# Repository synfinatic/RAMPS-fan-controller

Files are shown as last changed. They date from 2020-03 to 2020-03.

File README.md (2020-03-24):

# RAMPS v1.4 Fan and Analog Expansion Board

## Warning

This board is currently untested.  Manufacture & try at your own risk!

## What?

This board adds six (6) PWM controlled MOSFETs for controlling fans or LED's
and two analog inputs to your RAMPS v1.4 board.  It takes over the SERVOS and
AUX-1 ports on your RAMPS, leaving AUX-2 and AUX-3 available for other uses.

The board is designed to allow for +5-24V input to power your fans/LEDs/etc 
while the two analog connectors expose +5V from the RAMPS.

## Why?

I have a Flashforge Creator X (Makerbot Replicator 2X clone) with an additional
part cooling fan which I wanted to switch to using a RAMPS setup instead of the
rather outdated Mightyboard running Sailfish.  This printer supports dual extruders
so I wanted additional PWM controlled 24V outputs since the heated build plate and
hot ends would eat the 3 built into the RAMPS board.

Hence my config is:

 - Heated bulid plate: D8
 - E0 hot end: D9
 - E1 hot end: D10
 - E0 fan: D11 *
 - E1 fan: D6 *
 - Part cooling fan: D5 *
 - R channel on RGB Led: D4 *
 - G channel on RGB Led: D1 *
 - B channel on RGB Led: D0 *
 - E0 thermocouple amplifier: A4 *
 - E1 thermocouple amplifier: A3 *

* Notes connections to the expansion board

## Board Images

### Top
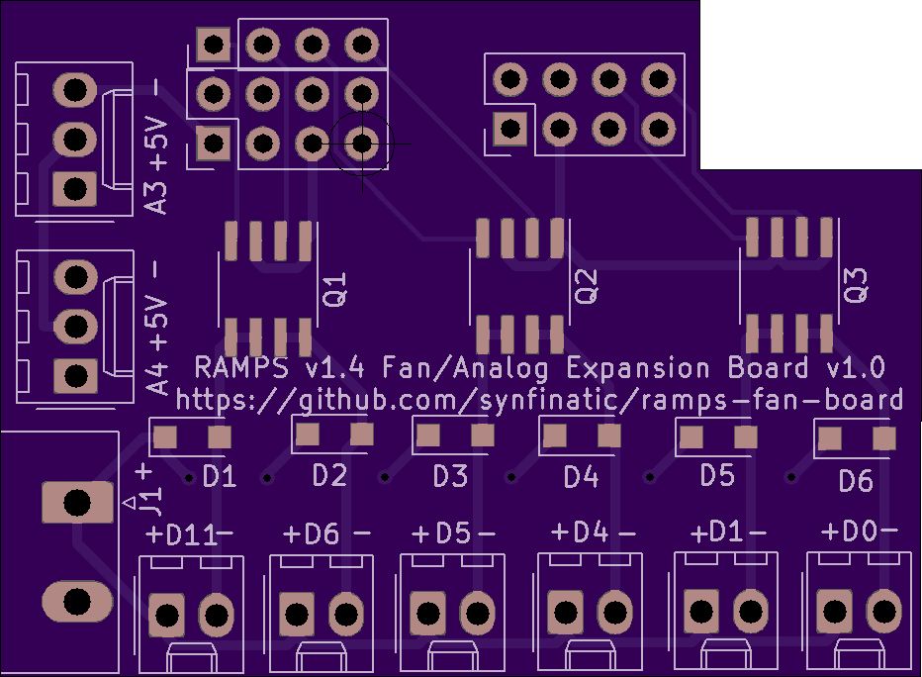
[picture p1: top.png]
top


### Bottom
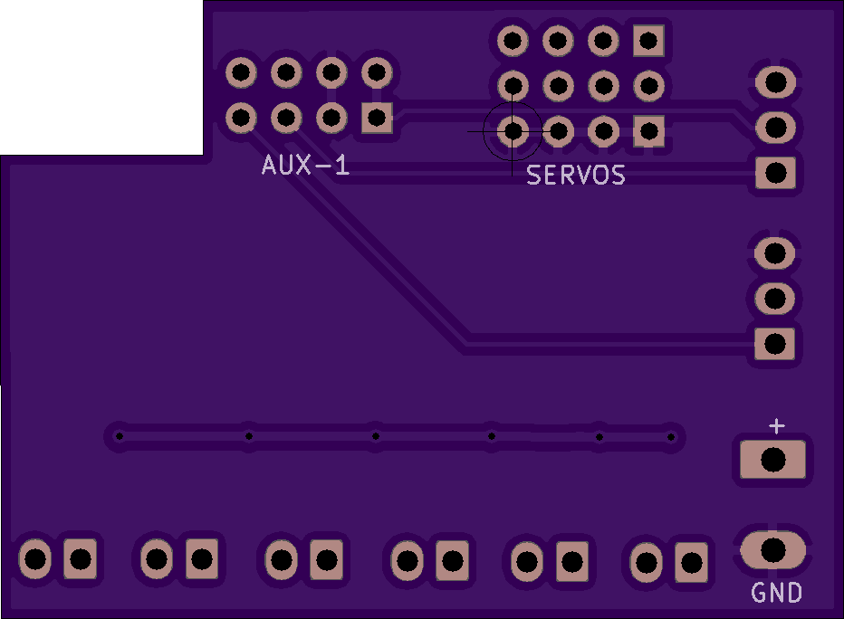
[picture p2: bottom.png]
bottom


### 3D Rendering
(Note the pins for the SERVOS and AUX-1 should be female headers on th _bottom_ of the board!)
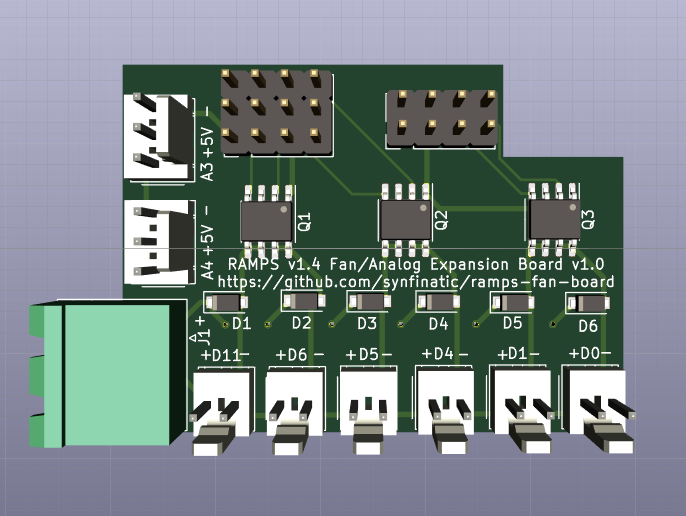
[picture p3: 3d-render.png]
3d render


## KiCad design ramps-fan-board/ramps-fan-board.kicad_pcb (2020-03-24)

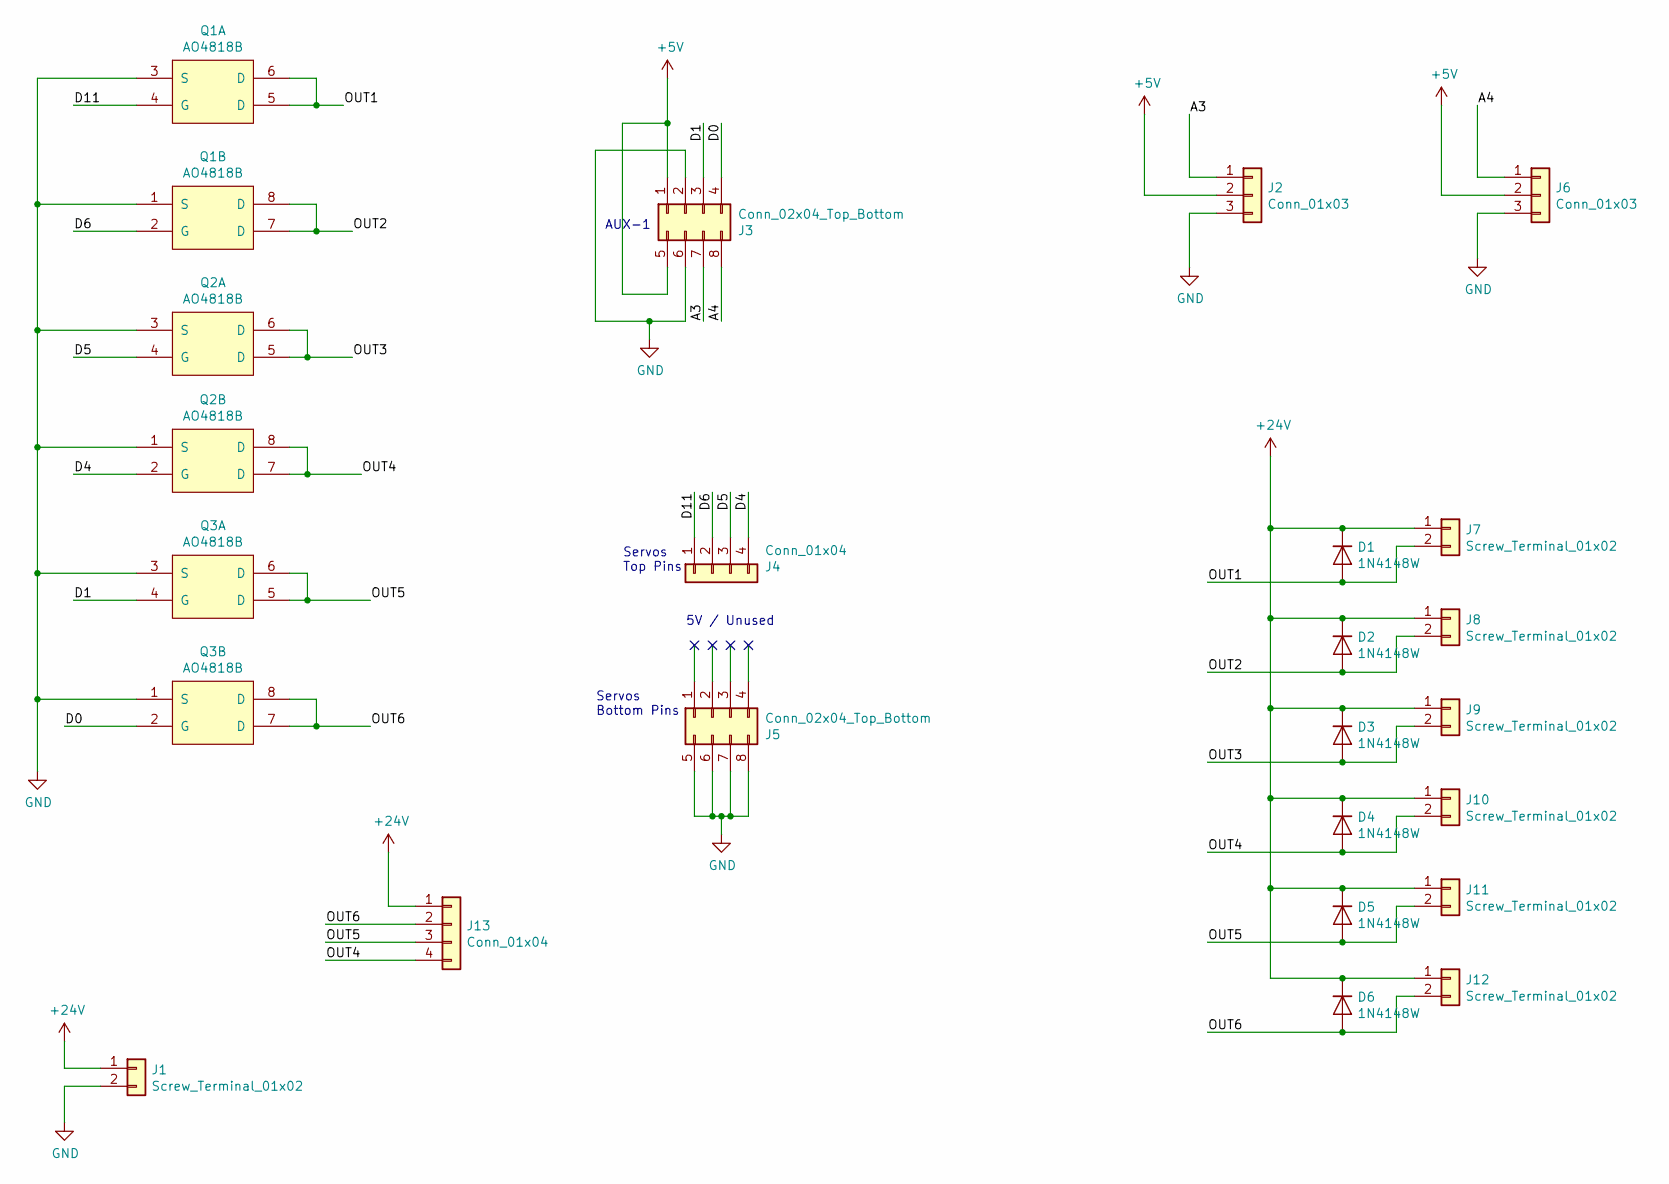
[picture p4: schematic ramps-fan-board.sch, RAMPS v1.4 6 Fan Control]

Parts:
D1, D2, D3, D4, D5, D6: 1N4148W; D_SOD-123F
J1: Screw_Terminal_01x02; PhoenixContact_MSTBA_2,5_2-G-5,08_1x02_P5.08mm_Horizontal
J2, J6: Conn_01x03; Molex_KK-254_AE-6410-03A_1x03_P2.54mm_Vertical
J3, J5: Conn_02x04_Top_Bottom; PinHeader_2x04_P2.54mm_Vertical
J4: Conn_01x04; PinHeader_1x04_P2.54mm_Vertical
J7, J8, J9, J10, J11, J12: Screw_Terminal_01x02; Molex_KK-254_AE-6410-02A_1x02_P2.54mm_Vertical
J13: Conn_01x04; Molex_KK-254_AE-6410-04A_1x04_P2.54mm_Vertical
Q1, Q2, Q3: AO4818B; SOIC-8_3.9x4.9mm_P1.27mm

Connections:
+5V: J2.2, J3.1, J3.5, J6.2
+24V: D1.1 (K), D2.1 (K), D3.1 (K), D4.1 (K), D5.1 (K), D6.1 (K), J1.1, J7.1, J8.1, J9.1, J10.1, J11.1, J12.1, J13.1
/A3: J2.1, J3.7
/A4: J3.8, J6.1
/D0: J3.4, Q3.2 (G)
/D1: J3.3, Q3.4 (G)
/D4: J4.4, Q2.2 (G)
/D5: J4.3, Q2.4 (G)
/D6: J4.2, Q1.2 (G)
/D11: J4.1, Q1.4 (G)
/OUT1: D1.2 (A), J7.2, Q1.5 (D), Q1.6 (D)
/OUT2: D2.2 (A), J8.2, Q1.7 (D), Q1.8 (D)
/OUT3: D3.2 (A), J9.2, Q2.5 (D), Q2.6 (D)
/OUT4: D4.2 (A), J10.2, J13.4, Q2.7 (D), Q2.8 (D)
/OUT5: D5.2 (A), J11.2, J13.3, Q3.5 (D), Q3.6 (D)
/OUT6: D6.2 (A), J12.2, J13.2, Q3.7 (D), Q3.8 (D)
GND: J1.2, J2.3, J3.2, J3.6, J5.5, J5.6, J5.7, J5.8, J6.3, Q1.1 (S), Q1.3 (S), Q2.1 (S), Q2.3 (S), Q3.1 (S), Q3.3 (S)

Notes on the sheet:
Servos Bottom Pins
Servos Top Pins
5V / Unused
AUX-1

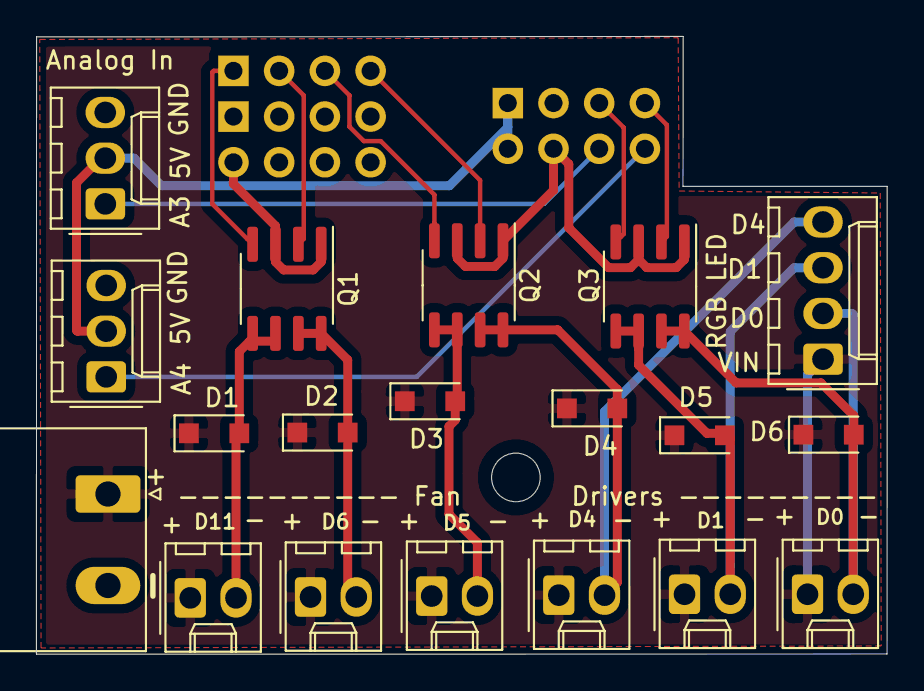
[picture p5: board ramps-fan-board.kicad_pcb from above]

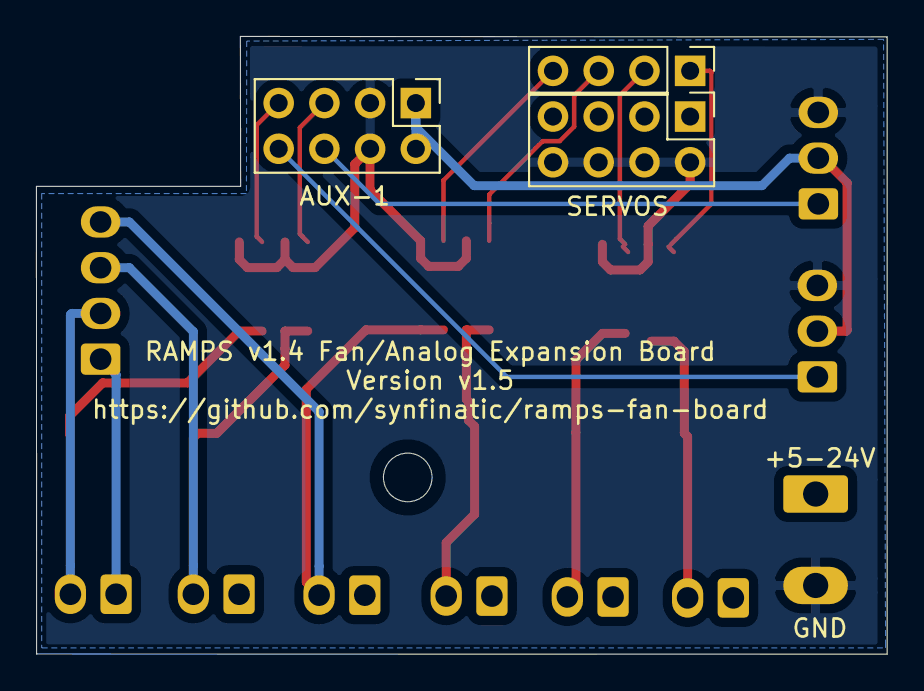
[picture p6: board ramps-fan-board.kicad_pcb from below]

Board: 2 copper layers, 47.3 x 34.3 mm, 22 parts (3 on the bottom side), 17 nets.

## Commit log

2020-03-23 Initial Release v1.0
    [ramps-fan-controller.kicad_pcb, ramps-fan-controller.sch]
2020-03-24 v1.5 (untested)
    Still waiting on the v1.0 PCB's back for testing, but updated things
    anyways.
    - Add dedicated RGB 4 pin header
    - Add Power plane on top of board
    - Move SERVOS and AUX-1 parts to the back of the board
    - Updated pin outs to correspond to flipping the parts
    - Improved silkscreening
    - Add 2.5mm standoff hole
    - Rename files to match the repo name
    [ramps-fan-board.kicad_pcb, ramps-fan-board.sch, ramps-fan-controller.kicad_pcb]
